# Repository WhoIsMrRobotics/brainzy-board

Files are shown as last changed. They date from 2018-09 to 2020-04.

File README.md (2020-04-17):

# Brainzy Board

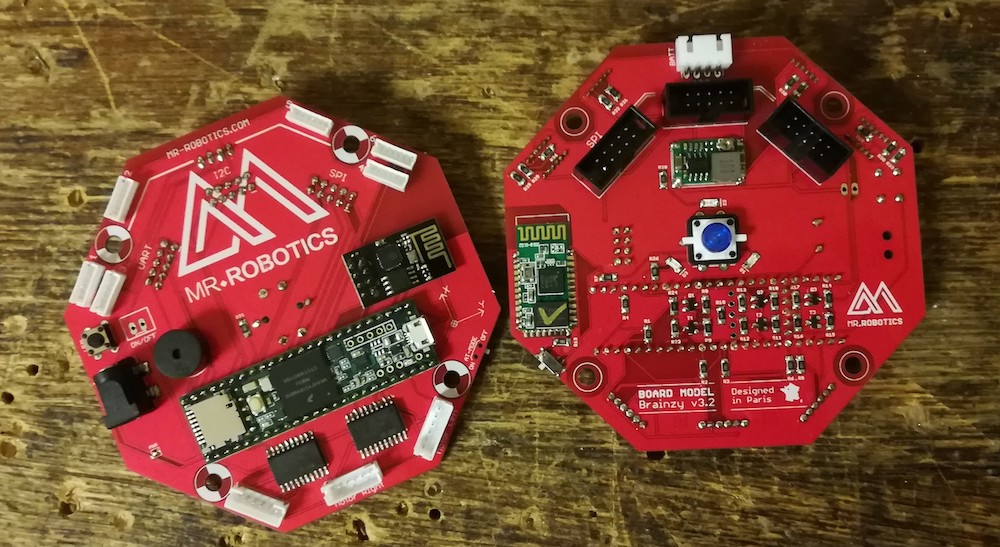
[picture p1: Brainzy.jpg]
Brainzy Board


Il s'agit d'une alternative aux cartes Arduino pour facilement construire son propre robot différentiel ou omnidirectionel. Basé sur une [Teensy 3.5](https://www.pjrc.com/store/teensy35.html), la Brainzy board se programme en C++ à travers l'[IDE Arduino](https://www.arduino.cc/en/Main/Software) à l'aide de la [bibliothèque Brainzy](https://github.com/WhoIsMrRobotics/brainzy-library). De nombreux modules peuvent être ajoutés à la carte pour étendre la complexité de vos créations.

Il existe deux types de modules :
* Les *Widgets*, dont la connection se fait par des connecteurs magnétiques et la communication via un bus I2C ;
* Les *extensions*, dont la connection se fait par des connecteurs standards et la communication via des bus SPI, UART, et/ou I2C.

Pour plus d'information, consultez notre site [www.mr-robotics.com](https://www.mr-robotics.com/).

**Caractéristiques de la Brainzy Board**

* *Mode d'utilisation :* 2 choix possibles pour le déplacement du robot : entrainement différenciel (2 roues) ou entrainement omnidirectionel (3 roues)
* *Dimensions de la carte :* 100mm x 100mm (forme hexagonale)
* *Moyens de communication :* USB, Bluetooth et Wifi

**Ports Entrées/Sorties**

* 1 port micro-USB
* 8 ports I2C, 3 ports SPI, 2 ports UART
* 3 ports pour des moteurs DC dotés de codeurs incrémentaux (deux channels)
* 1 lecteur de carte nano-SD
* 1 port pour vérifier l'état de charge de la batterie (jusqu'à 3 cellules)
* 1 Buzzer
* 1 interrupteur programmable
* 2 LEDs programmables

**Modules intégrés**

* 1 Module bluetooth (HC-05)
* 1 Module Wifi (ESP8266-01)

**Exemples de Widgets associés**

* IMU : accéléromètre 3 axes + gyroscope 3 axes (MPU-6050)
* Système d'éclairage : NeoPixels (WS2812B)
* Télémètre à ultrasons : Sonar (HC-SR04)
* Télémètre infrarouge : Sharp (GP2Y0A41SK0F)
* ...

**Exemples d'extensions associées**

* Bras poly-articulé
* Système de webcam pilotée
* Télécomande bluetooth
* Écran tactile
* ...

## Comment l'obtenir ?

Vous pouvez la commander en [nous contactant](mailto:bonjour@mr-robotics.com) ou suivre les étapes suivantes :
1. Réalisez le PCB à l'aide des fichiers GERBER.
2. Commandez les composants répertoriés dans le fichier BOM, puis soudez les.
3. Soudez une Teensy 3.5 en faisant attention aux indications suivantes.
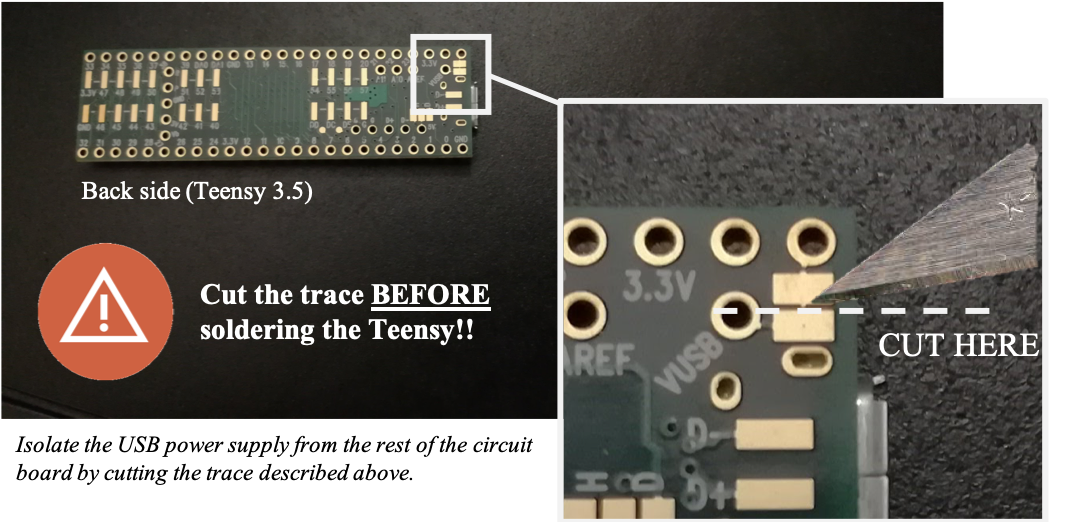
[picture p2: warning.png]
Warning cut VUSB trace


## Quelques tutoriels

* Pour obtenir un modèle CAO de la carte, consultez [ce lien](https://www.youtube.com/watch?v=ekHAkWB-WTM).
* Pour générer les fichiers Gerber nécessaire à la production du PCB, consultez [ce lien](https://learn.sparkfun.com/tutorials/designing-pcbs-advanced-smd/gerber-generation).

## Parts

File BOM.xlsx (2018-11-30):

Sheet: PCB - Brainzy 3.2.1
PCB
Size | 10cm x 10cm
Soldermask Color | Red
Silkscreen Legend Color | White
Thickness | 1.6mm
Penalization | Single board, no penalization
Layer | 2
Quantity | 100
Outer Copper Thickness | 1oz, 35um
Surface Finish | HASL
Material | FR4
Smallest Hole | 0.25mm
Min. Tracing/Spacing | 0.15mm
PCBA
Number of SMD items | 62
Number of TH items | 18
Number of BGA / QFN / Leadless items | 0
Quantity | 100

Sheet: BOM - Brainzy 3.2.1
Manufacturer | Manufacturer Part Number | Designator | Qty | Description | Case | SMD, BGA, LCC, or TH | Top/Bottom | Points | Total points | Comment
Yageo | RC1206FR-071KL | R1; R2; R3; R4; R5; R6; R20 | 7 | Résistance 1k (tolérence 1%) | 1206 | SMD | Bottom | 2 | 14
Yageo | RC1206FR-0710KL | R22 | 1 | Résistance 10k (tolérence 1%) | 1206 | SMD | Bottom | 2 | 2
Yageo | RC1206FR-0710KL | R19 | 1 | Résistance 10k (tolérence 1%) | 1206 | SMD | Top | 2 | 2
Yageo | RC1206FR-07470KL | R8; R9; R10; R11; R12; R14; R15; R16; R18; R24; R25; R30; R31; R34; R35 | 15 | Résistance 470k (tolérence 1%) | 1206 | SMD | Bottom | 2 | 30
Yageo | RC1206FR-07150KL | R13; R17; R23; R28; R29; R32; R33; R36 | 8 | Résistance 150k (tolérence 1%) | 1206 | SMD | Bottom | 2 | 16
Yageo | RC1206FR-07470RL | R7; R26 | 2 | Résistance 470 (tolérence 1%) | 1206 | SMD | Bottom | 2 | 4
Yageo | RC1206FR-07470RL | R21 | 1 | Résistance 470 (tolérence 1%) | 1206 | SMD | Top | 2 | 2
ON Semiconductor | BSS84LT1G | T1; T2; T3 | 3 | Mosfet canal P | SOT23 | SMD | Bottom | 3 | 9
ON Semiconductor | BSS138LT1G | Q1; Q2; Q3 | 3 | Mosfet canal N | SOT23 | SMD | Bottom | 3 | 9
TE Connectivity | MLL1200S | S1 | 1 | Commutateur à glissière |  | SMD | Bottom | 7 | 7
DIALIGHT | 598-8210-107F | D2 | 1 | Led rouge | 1206 | SMD | Bottom | 2 | 2
DIALIGHT | 598-8291-107F | D3 | 1 | Led bleu | 1206 | SMD | Bottom | 2 | 2
DIALIGHT | 598-8270-107F | D1 | 1 | Led verte | 1206 | SMD | Bottom | 2 | 2
STMicroelectronics | L293DD | U1; U2 | 2 | Pont en H | SOIC-20 | SMD | Top | 20 | 40
JST | B6B-ZR(LF)(SN) | SENSOR1; SENSOR2; SENSOR3; SENSOR4; SENSOR5; SENSOR6 | 6 | Connecteur ZH 6 pins | - | TH | Top | 6 | 36
JST | B6B-PH-K-S(LF)(SN) | MOT_LEFT; MOT_RIGHT; MOT_FRONT | 3 | Connecteur PH 6 pins | - | TH | Top | 6 | 18
JST | S4B-XH-A(LF)(SN) | BATT | 1 | Connecteur XH 4 pins coudé | - | TH | Bottom | 4 | 4
JST | B2B-XH-A(LF)(SN) | ON/OFF | 0 | Connecteur XH 2 pins | - | TH | Top | 2 | 0
Würth Elektronik | 694108106102 | J7 | 1 | Connecteur jack alimentation | - | SMD | Top | 4 | 4
C&K Components | PTS645SL43-2-LFS | RST | 1 | Intérupteur | - | TH | Top | 4 | 4
Amphenol | T821110A1S100CEU | EXT1; EXT2; EXT3 | 3 | Connecteur 5x2 pins | - | TH | Bottom | 10 | 30
IMO PRECISION CONTROLS | 41.T70P015H-LF | LS1 | 1 | Transducteur passif | - | TH | Top | 2 | 2
HC | HC-05 | U3 | 1 | Module bluetooth | - | SMD | Bottom | 34 | 34 | Must be a HC-05 (not a HC-06)
Espressif Systems | ESP8266 (ESP-01) | U$6 | 1 | Module Wifi | - | TH | Top | 8 | 8
PJRC | Teensy 3.5 | U$1 | 1 | Microcontrôleur | - | TH | Top | 53 | 53 | https://www.pjrc.com/store/teensy35.html (Cut the VUSB trace before soldering the Teensy)
? | TSD1265 | S2 | 1 | Bouton LED bleu | - | TH | Bottom | 6 | 6 | https://www.sparkfun.com/products/10443
Monolithic Power Systems | MP2307DN-LF | BK | 1 | - | SOIC8N | SMD | Bottom | 8 | 8
Kemet | C1210C106M4PACTU | C4; C5 | 2 | Condensateur 10uF en céramique | 1210 | SMD | Bottom | 2 | 4
AVX | 06031C103K4Z2A | C6 | 1 | Condensateur 10nF | 0603 | SMD | Bottom | 2 | 2
AVX | 0603YC104K4T4A | C3 | 1 | Condensateur 0.1uF | 0603 | SMD | Bottom | 2 | 2
AVX | 06035C332KAT2A | C7 | 1 | Condensateur 3.3nF | 0603 | SMD | Bottom | 2 | 2
Yageo | CC0805MKX5R5BB226 | C1; C2 | 2 | Condensateur 22uF en céramique | 0805 | SMD | Bottom | 2 | 4
Abracon | ASPI-0630LR-100M-T15 | L1 | 1 | Inductance 10uH | 0630 | SMD | Bottom | 2 | 2
Vishay | CRCW0603100KFKEA | R39 | 1 | Résistance 100k (tolérence 1%) | 0603 | SMD | Bottom | 2 | 2
Vishay | CRCW060344K2FKEA | R38 | 1 | Résistance 44,2k (tolérence 1%) | 0603 | SMD | Bottom | 2 | 2
Vishay | CRCW060310K0FKEA | R37 | 1 | Résistance 10k (tolérence 1%) | 0603 | SMD | Bottom | 2 | 2
Vishay | CRCW06036K80FKEA | R27 | 1 | Résistance 6.8k (tolérence 1%) | 0603 | SMD | Bottom | 2 | 2

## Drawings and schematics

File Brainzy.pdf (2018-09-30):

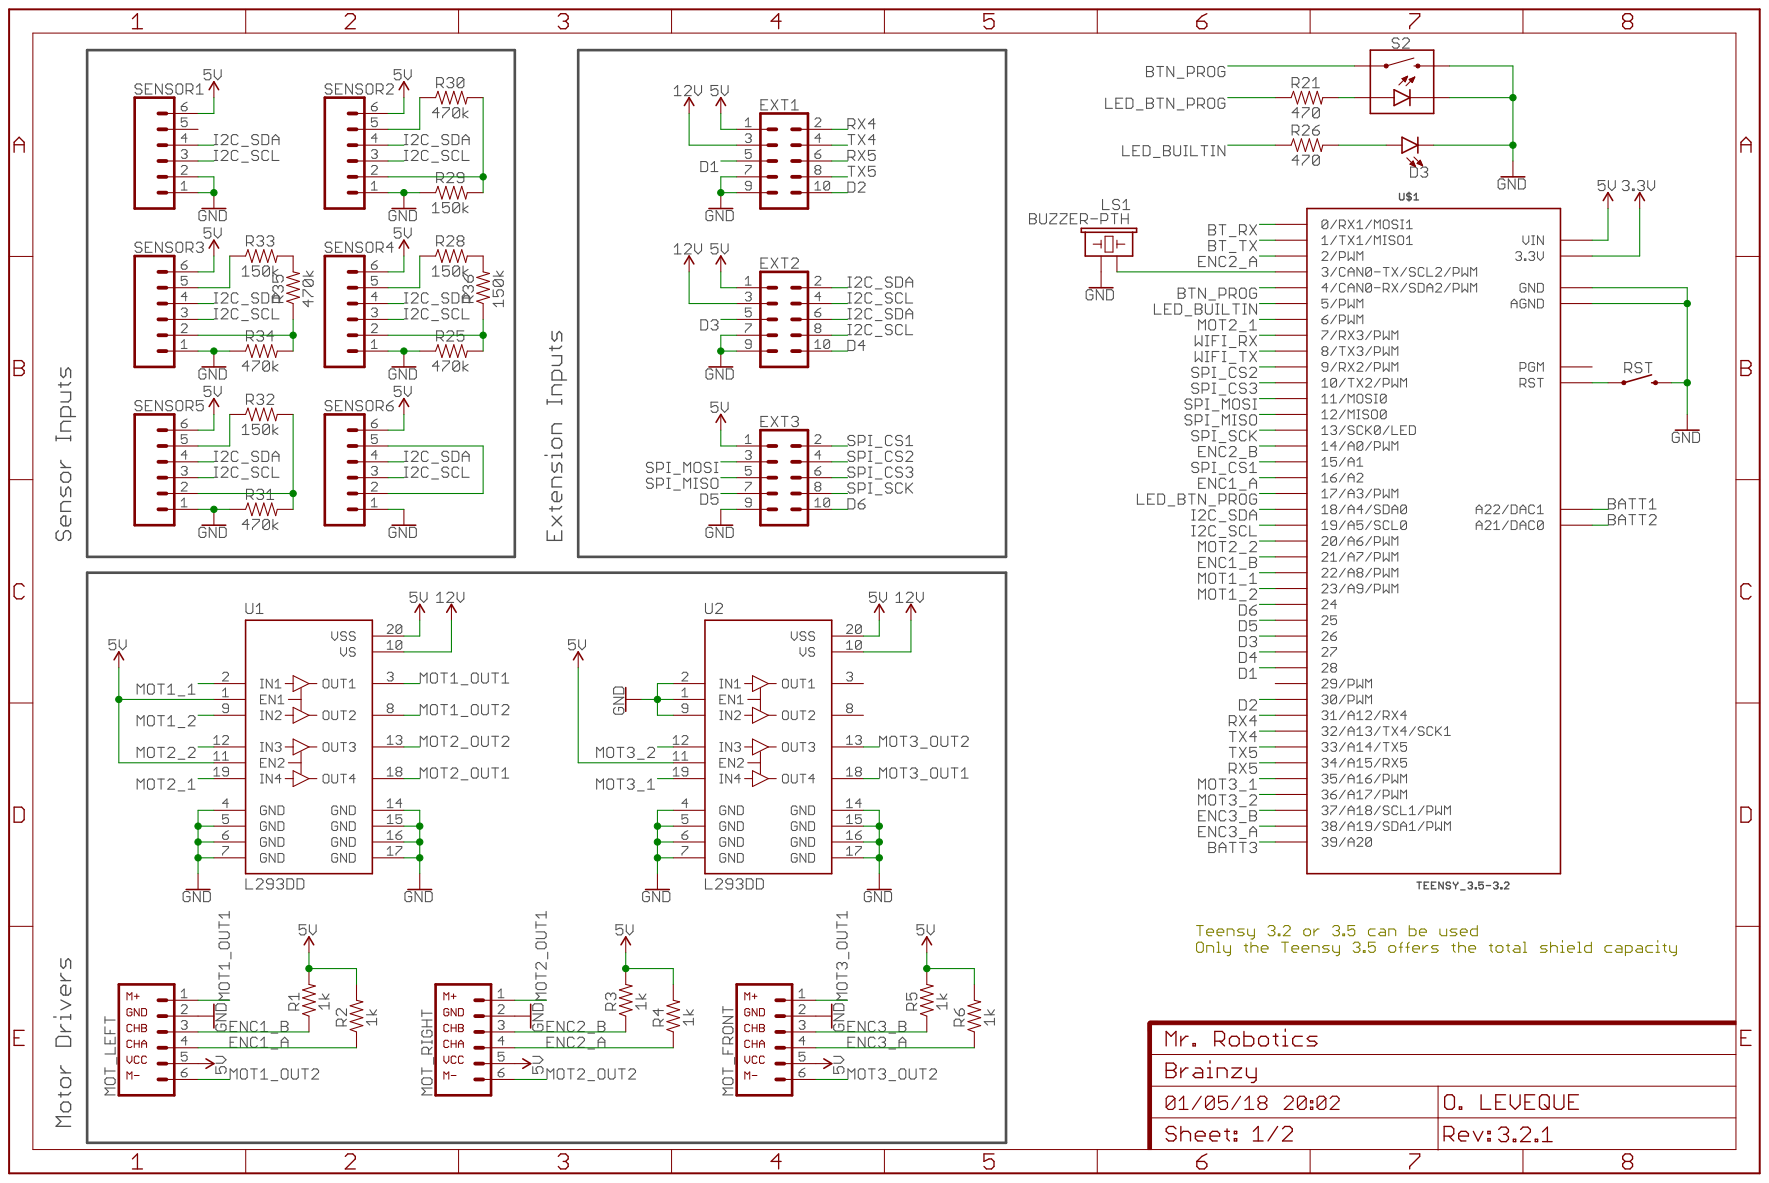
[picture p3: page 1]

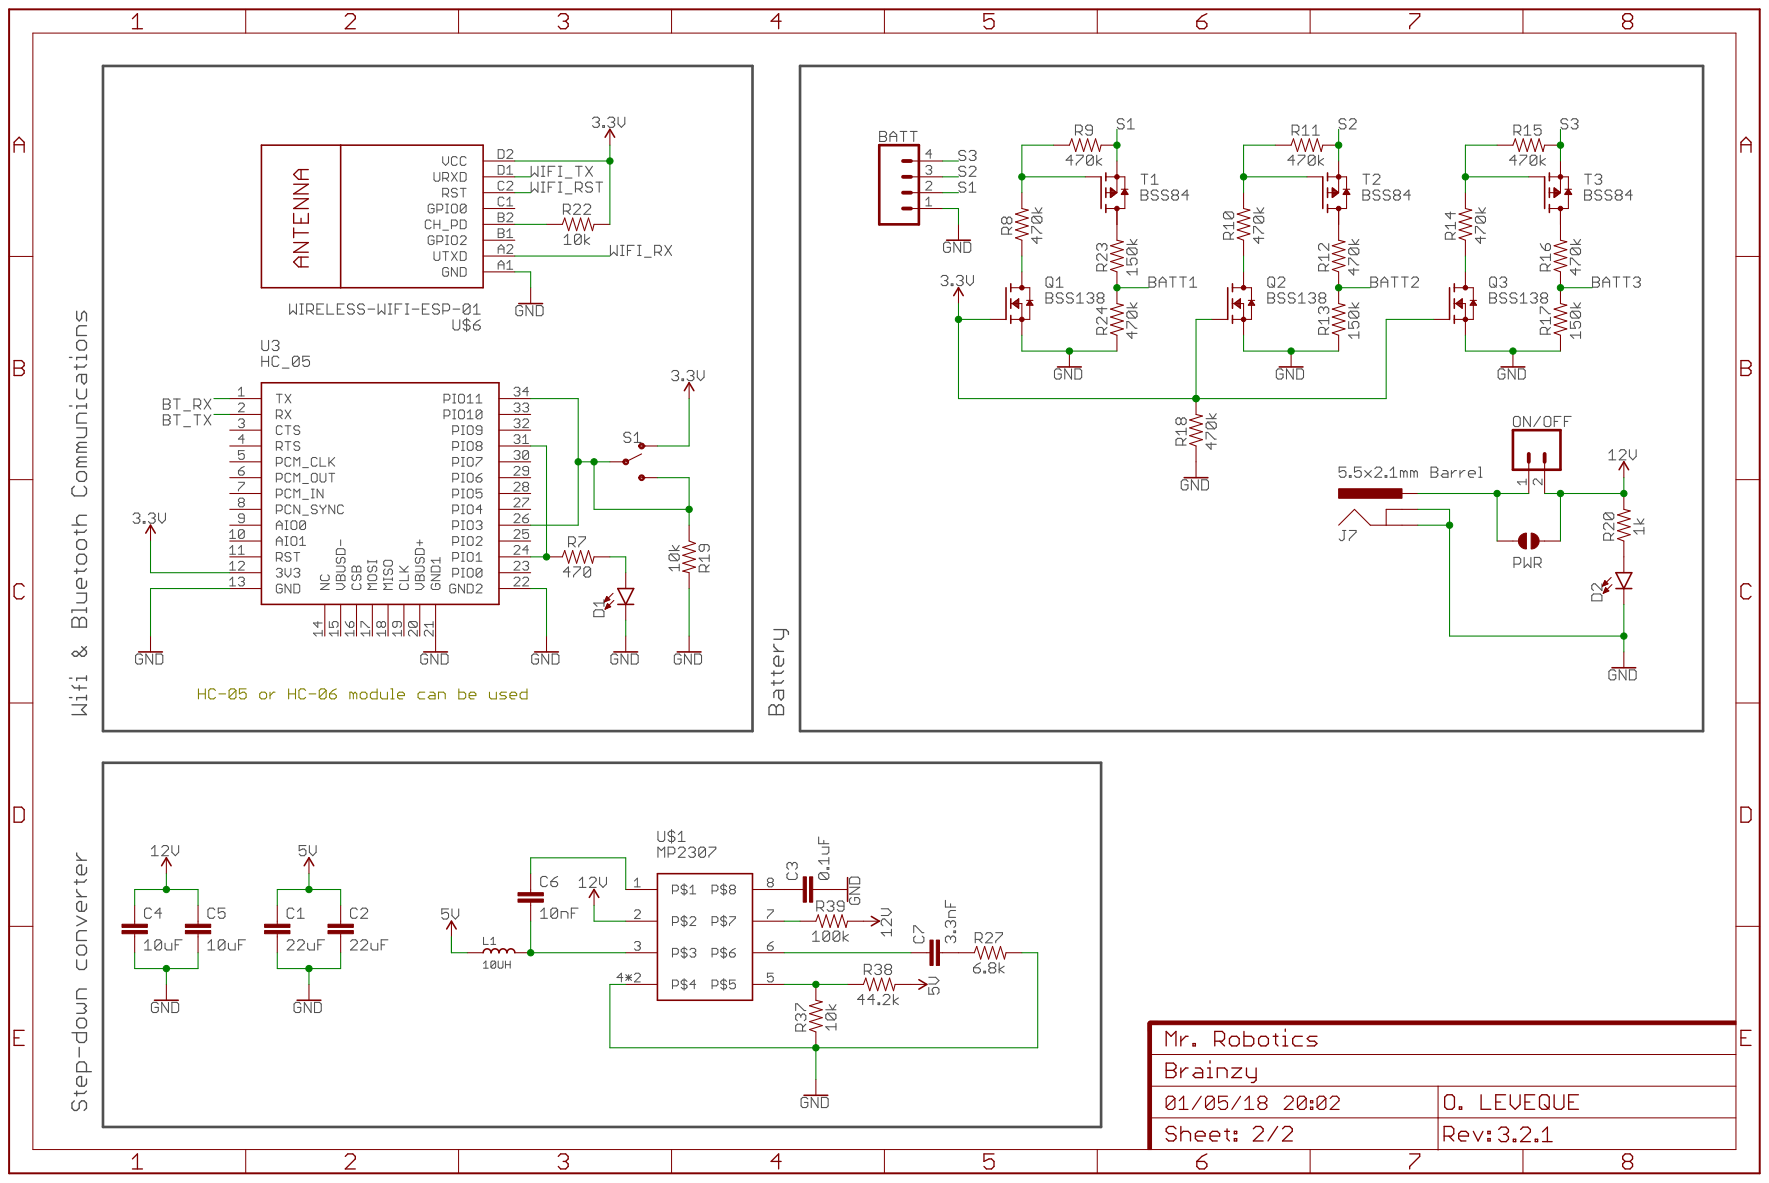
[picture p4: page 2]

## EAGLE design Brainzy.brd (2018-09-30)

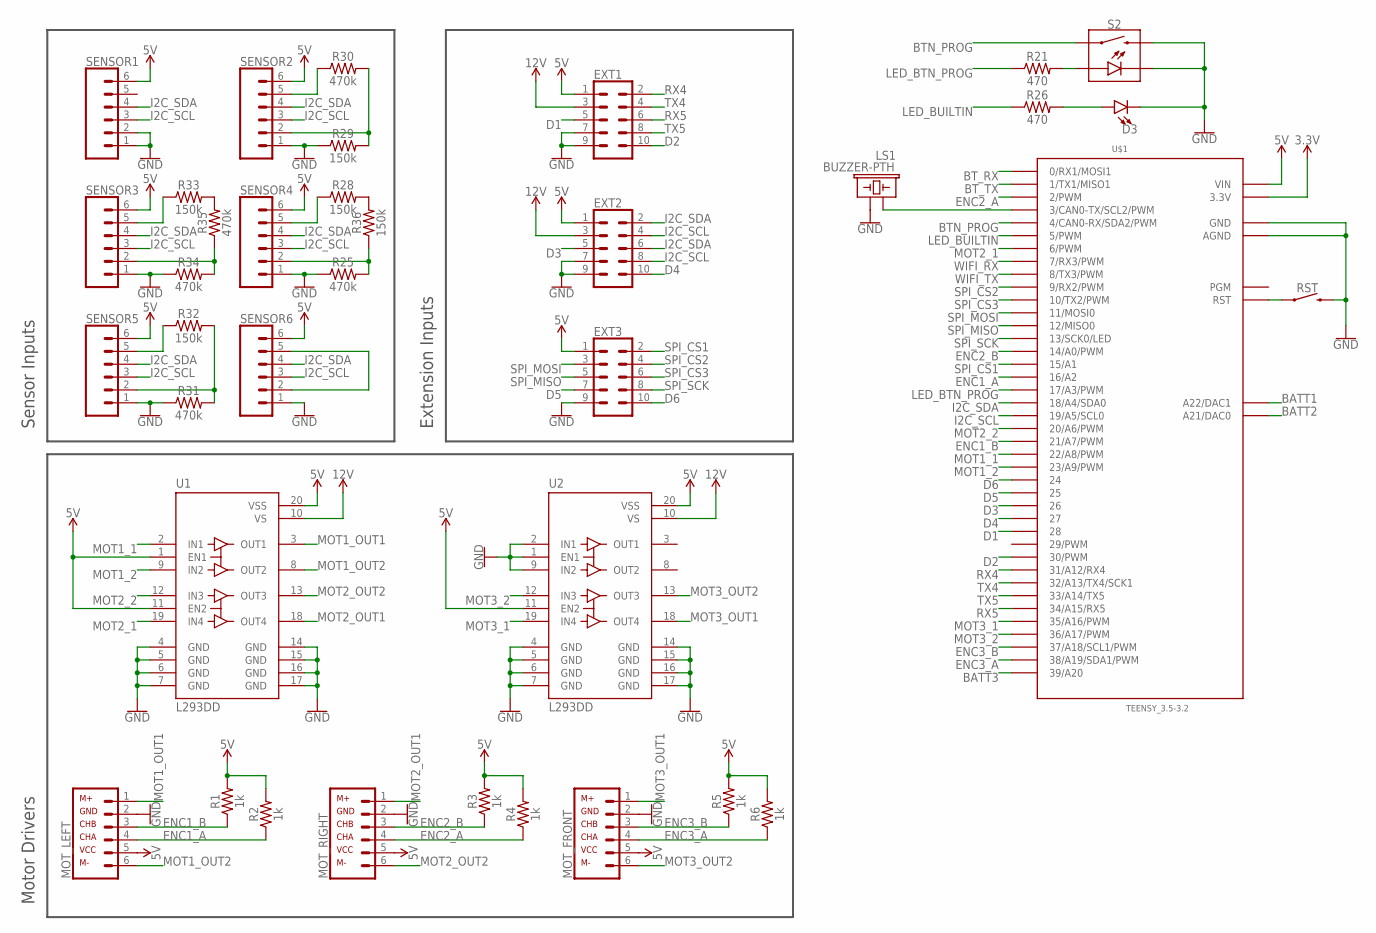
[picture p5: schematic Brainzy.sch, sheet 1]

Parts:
D3: LED-FKIT-1206; FKIT-LED-1206
EXT1, EXT2, EXT3: CONN_05X2SHD_LOCK; 2X5-SHROUDED_LOCK
LS1: BUZZER-PTH; BUZZER-12MM
MOT_FRONT: DC-MOTOR-CONNECTOR; JST-PH6
MOT_LEFT: DC-MOTOR-CONNECTOR; JST-PH6
MOT_RIGHT: DC-MOTOR-CONNECTOR; JST-PH6
R1, R2, R3, R4, R5, R6: 1k; 1206
R21, R26: 470; 1206
R25, R30, R31, R34, R35: 470k; 1206
R28, R29, R32, R33, R36: 150k; 1206
RST: MOMENTARY-SWITCH-SPST-PTH-6.0MM; TACTILE_SWITCH_PTH_6.0MM
S2: MOMENTARY-SWITCH-SPST-LED-PTH-12MM; TACTILE_SWITCH_LED_PTH_12MM
SENSOR1, SENSOR2, SENSOR3, SENSOR4, SENSOR5, SENSOR6: JST-ZH6
U1, U2: L293DD; SOIC127P1033X265-20N
U$1: TEENSY_3.5-3.2

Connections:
3.3V: U$1.3.3V, U$1.3.3V1 (3.3V), U$1.3.3V2 (3.3V), U$1.3.3V3 (3.3V); also elsewhere on the board
5V: EXT1.1, EXT2.1, EXT3.1, MOT_FRONT.5 (5-CHA), MOT_LEFT.5 (5-CHA), MOT_RIGHT.5 (5-CHA), R1.2, R2.2, R3.2, R4.2, R5.2, R6.2, SENSOR1.6, SENSOR2.6, SENSOR3.6, SENSOR4.6, SENSOR5.6, SENSOR6.6, U1.1 (EN1), U1.11 (EN2), U1.20 (VSS), U2.11 (EN2), U2.20 (VSS), U$1.VIN; also elsewhere on the board
12V: EXT1.3, EXT2.3, U1.10 (VS), U2.10 (VS); also elsewhere on the board
BATT1: U$1.A22 (A22/DAC1); also elsewhere on the board
BATT2: U$1.A21 (A21/DAC0); also elsewhere on the board
BATT3: U$1.39/A20; also elsewhere on the board
BTN_PROG: S2.4 (1), U$1.4 (4/CAN0-RX/SDA2/PWM)
BT_RX: U$1.0 (0/RX1/MOSI1); also elsewhere on the board
BT_TX: U$1.1 (1/TX1/MISO1); also elsewhere on the board
BUZZER: LS1.+ (1), U$1.3 (3/CAN0-TX/SCL2/PWM)
D1: EXT1.5, U$1.28
D2: EXT1.10, U$1.30 (30/PWM)
D3: EXT2.5, U$1.26
D4: EXT2.10, U$1.27
D5: EXT3.7, U$1.25
D6: EXT3.10, U$1.24
ENC1_A: MOT_LEFT.4 (4-GND), R2.1, U$1.16/A2
ENC1_B: MOT_LEFT.3 (3-VCC), R1.1, U$1.21/A7 (21/A7/PWM)
ENC2_A: MOT_RIGHT.4 (4-GND), R4.1, U$1.2 (2/PWM)
ENC2_B: MOT_RIGHT.3 (3-VCC), R3.1, U$1.14/A0 (14/A0/PWM)
ENC3_A: MOT_FRONT.4 (4-GND), R6.1, U$1.38/A19 (38/A19/SDA1/PWM)
ENC3_B: MOT_FRONT.3 (3-VCC), R5.1, U$1.37/A18 (37/A18/SCL1/PWM)
GND: D3.C, EXT1.7, EXT1.9, EXT2.7, EXT2.9, EXT3.9, LS1.- (2), MOT_FRONT.2 (2-M+), MOT_LEFT.2 (2-M+), MOT_RIGHT.2 (2-M+), R25.1, R29.1, R31.1, R34.1, RST.3 (2), S2.2, S2.C, SENSOR1.1, SENSOR1.2, SENSOR2.1, SENSOR3.1, SENSOR4.1, SENSOR5.1, SENSOR6.1, U1.4 (GND), U1.5 (GND), U1.6 (GND), U1.7 (GND), U1.14 (GND), U1.15 (GND), U1.16 (GND), U1.17 (GND), U2.1 (EN1), U2.2 (IN1), U2.4 (GND), U2.5 (GND), U2.6 (GND), U2.7 (GND), U2.9 (IN2), U2.14 (GND), U2.15 (GND), U2.16 (GND), U2.17 (GND), U$1.AGND, U$1.GND, U$1.GND1 (GND), U$1.GND2 (GND), U$1.GND3 (GND); also elsewhere on the board
I2C_SCL: EXT2.4, EXT2.8, SENSOR1.3, SENSOR2.3, SENSOR3.3, SENSOR4.3, SENSOR5.3, SENSOR6.3, U$1.19/A5 (19/A5/SCL0)
I2C_SDA: EXT2.2, EXT2.6, SENSOR1.4, SENSOR2.4, SENSOR3.4, SENSOR4.4, SENSOR5.4, SENSOR6.4, U$1.18/A4 (18/A4/SDA0)
LED_BTN_PROG: R21.1, U$1.17/A3 (17/A3/PWM)
LED_BUILTIN: R26.1, U$1.5 (5/PWM)
MOT1_1: U1.2 (IN1), U$1.22/A8 (22/A8/PWM)
MOT1_2: U1.9 (IN2), U$1.23/A9 (23/A9/PWM)
MOT1_OUT1: MOT_LEFT.1 (1-M-), U1.3 (OUT1)
MOT1_OUT2: MOT_LEFT.6 (6-CHB), U1.8 (OUT2)
MOT2_1: U1.19 (IN4), U$1.6 (6/PWM)
MOT2_2: U1.12 (IN3), U$1.20/A6 (20/A6/PWM)
MOT2_OUT1: MOT_RIGHT.1 (1-M-), U1.18 (OUT4)
MOT2_OUT2: MOT_RIGHT.6 (6-CHB), U1.13 (OUT3)
MOT3_1: U2.19 (IN4), U$1.35/A16 (35/A16/PWM)
MOT3_2: U2.12 (IN3), U$1.36/A17 (36/A17/PWM)
MOT3_OUT1: MOT_FRONT.1 (1-M-), U2.18 (OUT4)
MOT3_OUT2: MOT_FRONT.6 (6-CHB), U2.13 (OUT3)
unnamed: D3.A, R26.2
unnamed: R21.2, S2.A
unnamed: SENSOR6.2, SENSOR6.5
unnamed: R25.2, R36.1, SENSOR4.2
unnamed: R28.1, SENSOR4.5
unnamed: R31.2, R32.2, SENSOR5.2
unnamed: R32.1, SENSOR5.5
unnamed: R29.2, R30.2, SENSOR2.2
unnamed: R30.1, SENSOR2.5
unnamed: R33.2, R35.2
unnamed: R34.2, R35.1, SENSOR3.2
unnamed: R33.1, SENSOR3.5
unnamed: R28.2, R36.2
RST: RST.1, U$1.RST_3.5 (RST)
RX4: EXT1.2, U$1.31/A12 (31/A12/RX4)
RX5: EXT1.6, U$1.34/A15 (34/A15/RX5)
SPI_CS1: EXT3.2, U$1.15/A1
SPI_CS2: EXT3.4, U$1.9 (9/RX2/PWM)
SPI_CS3: EXT3.6, U$1.10 (10/TX2/PWM)
SPI_MISO: EXT3.5, U$1.12 (12/MISO0)
SPI_MOSI: EXT3.3, U$1.11 (11/MOSI0)
SPI_SCK: EXT3.8, U$1.13 (13/SCK0/LED)
TX4: EXT1.4, U$1.32/A13 (32/A13/TX4/SCK1)
TX5: EXT1.8, U$1.33/A14 (33/A14/TX5)
WIFI_RX: U$1.7 (7/RX3/PWM); also elsewhere on the board
WIFI_TX: U$1.8 (8/TX3/PWM); also elsewhere on the board

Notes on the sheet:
Motor Drivers
Sensor Inputs
Extension Inputs

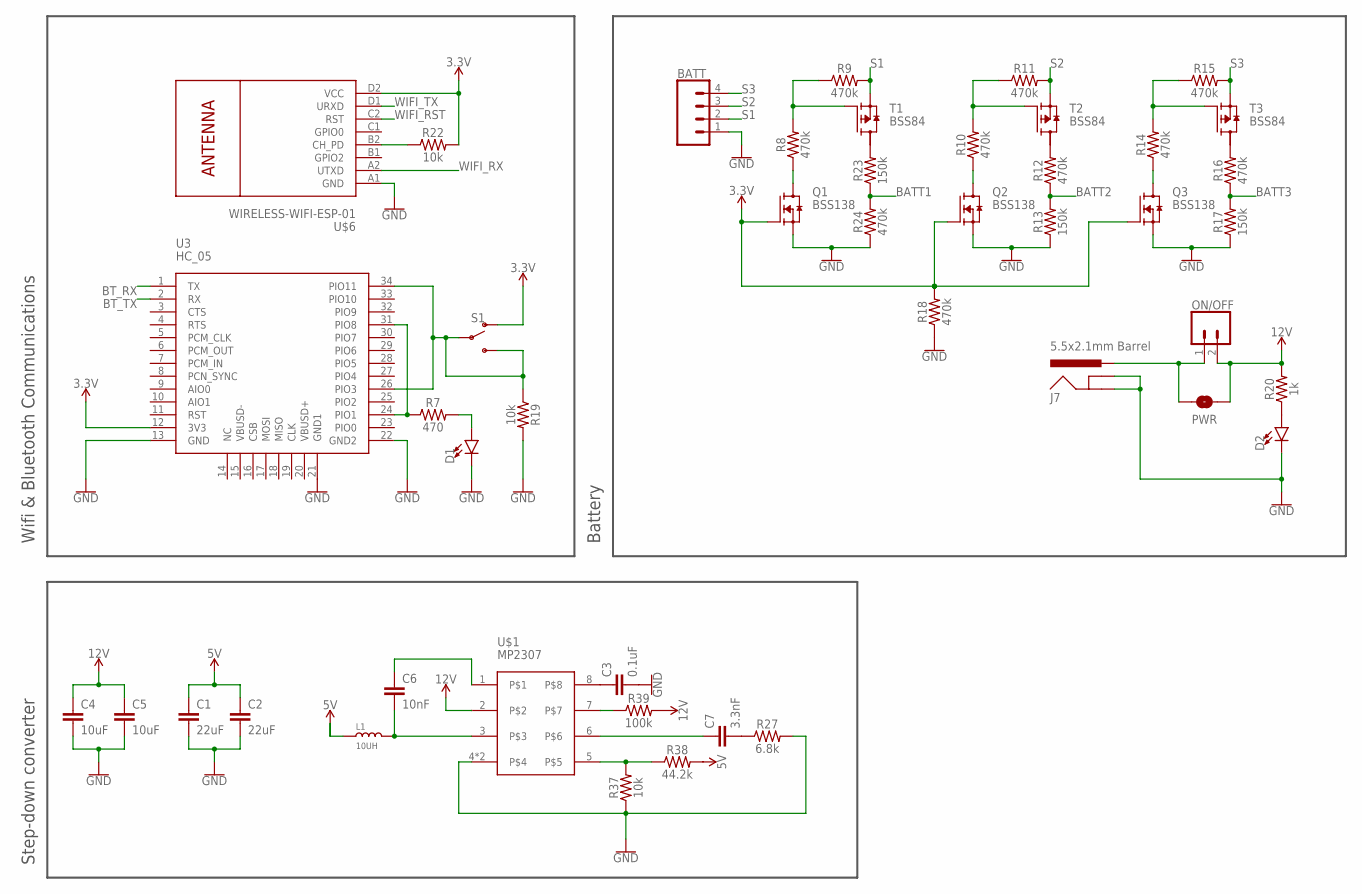
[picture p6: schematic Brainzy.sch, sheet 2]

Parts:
BATT: CONN_04LOCK_LONGPADS; 1X04_LOCK_LONGPADS
BK: MP2307; SOIC127P600X170-9N
C1, C2: 22uF; 0805
C3: 0.1uF; 0603
C4, C5: 10uF; 1210
C6: 10nF; 0603
C7: 3.3nF; 0603
D1, D2: LED-FKIT-1206; FKIT-LED-1206
J7: 5.5x2.1mm Barrel; POWER_JACK_SMD
L1: 10UH; SMD-2P-L6.0XW6.0XH3.0MM
ON/OFF: JST-XH-02-PIN-LONG-PAD; JST-XH-02-PACKAGE-LONG-PAD
PWR: JUMPER-SMT_2_NO_SILK; SMT-JUMPER_2_NO_SILK
Q1, Q2, Q3: BSS138; SOT23
R7: 470; 1206
R8, R9, R10, R11, R12, R14, R15, R16, R18, R24: 470k; 1206
R13, R17, R23: 150k; 1206
R19, R22: 10k; 1206
R20: 1k; 1206
R27: 6.8k; 0603
R37: 10k; 0603
R38: 44.2k; 0603
R39: 100k; 0603
S1: SWITCH-SPDT-SMD-RIGHT-ANGLE; SWITCH_SPST_SMD_A
T1, T2, T3: BSS84; SOT23
U3: HC_05; BLUETOOTH_SMD
U$6: WIRELESS-WIFI-ESP-01

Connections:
3.3V: Q1.1 (G), Q2.1 (G), Q3.1 (G), R18.2, R22.2, S1.1 (O), U3.12 (3V3), U$6.D2 (VCC); also elsewhere on the board
5V: C1.1, C2.1, L1.1, R38.2; also elsewhere on the board
12V: BK.2, C4.1, C5.1, ON/OFF.2, PWR.2, R20.2, R39.2; also elsewhere on the board
BATT1: R23.1, R24.2; also elsewhere on the board
BATT2: R12.1, R13.2; also elsewhere on the board
BATT3: R16.1, R17.2; also elsewhere on the board
BT_RX: U3.1 (TX); also elsewhere on the board
BT_TX: U3.2 (RX); also elsewhere on the board
GND: BATT.1, BK.4, BK.9, C1.2, C2.2, C3.2, C4.2, C5.2, D1.C, D2.C, J7.GND (GNDBREAK), J7.P$4 (GND), Q1.2 (S), Q2.2 (S), Q3.2 (S), R13.1, R17.1, R18.1, R19.2, R24.1, R27.2, R37.1, U3.13 (GND), U3.21 (GND1), U3.22 (GND2), U$6.A1 (GND); also elsewhere on the board
unnamed: R12.2, T2.3 (D)
unnamed: D2.A, R20.1
unnamed: R22.1, U$6.B2 (CH_PD)
unnamed: R8.2, R9.1, T1.1 (G)
unnamed: Q1.3 (D), R8.1
unnamed: R16.2, T3.3 (D)
unnamed: R10.2, R11.1, T2.1 (G)
unnamed: BK.7, R39.1
unnamed: R7.1, U3.24 (PIO1), U3.31 (PIO8)
unnamed: D1.A, R7.2
unnamed: Q2.3 (D), R10.1
unnamed: R14.2, R15.1, T3.1 (G)
unnamed: Q3.3 (D), R14.1
unnamed: J7.VIN0 (PWR), ON/OFF.1, PWR.1
unnamed: R19.1, S1.2, S1.3 (S), U3.26 (PIO3), U3.34 (PIO11)
unnamed: R23.2, T1.3 (D)
unnamed: BK.5, R37.2, R38.1
unnamed: BK.8, C3.1
unnamed: BK.6, C7.1
unnamed: BK.3, C6.2, L1.2
unnamed: C7.2, R27.1
unnamed: BK.1, C6.1
S1: BATT.2, R9.2, T1.2 (S)
S2: BATT.3, R11.2, T2.2 (S)
S3: BATT.4, R15.2, T3.2 (S)
WIFI_RST: U$6.C2 (RST)
WIFI_RX: U$6.A2 (UTXD); also elsewhere on the board
WIFI_TX: U$6.D1 (URXD); also elsewhere on the board

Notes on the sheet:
Wifi & Bluetooth Communications
Battery
Step-down converter

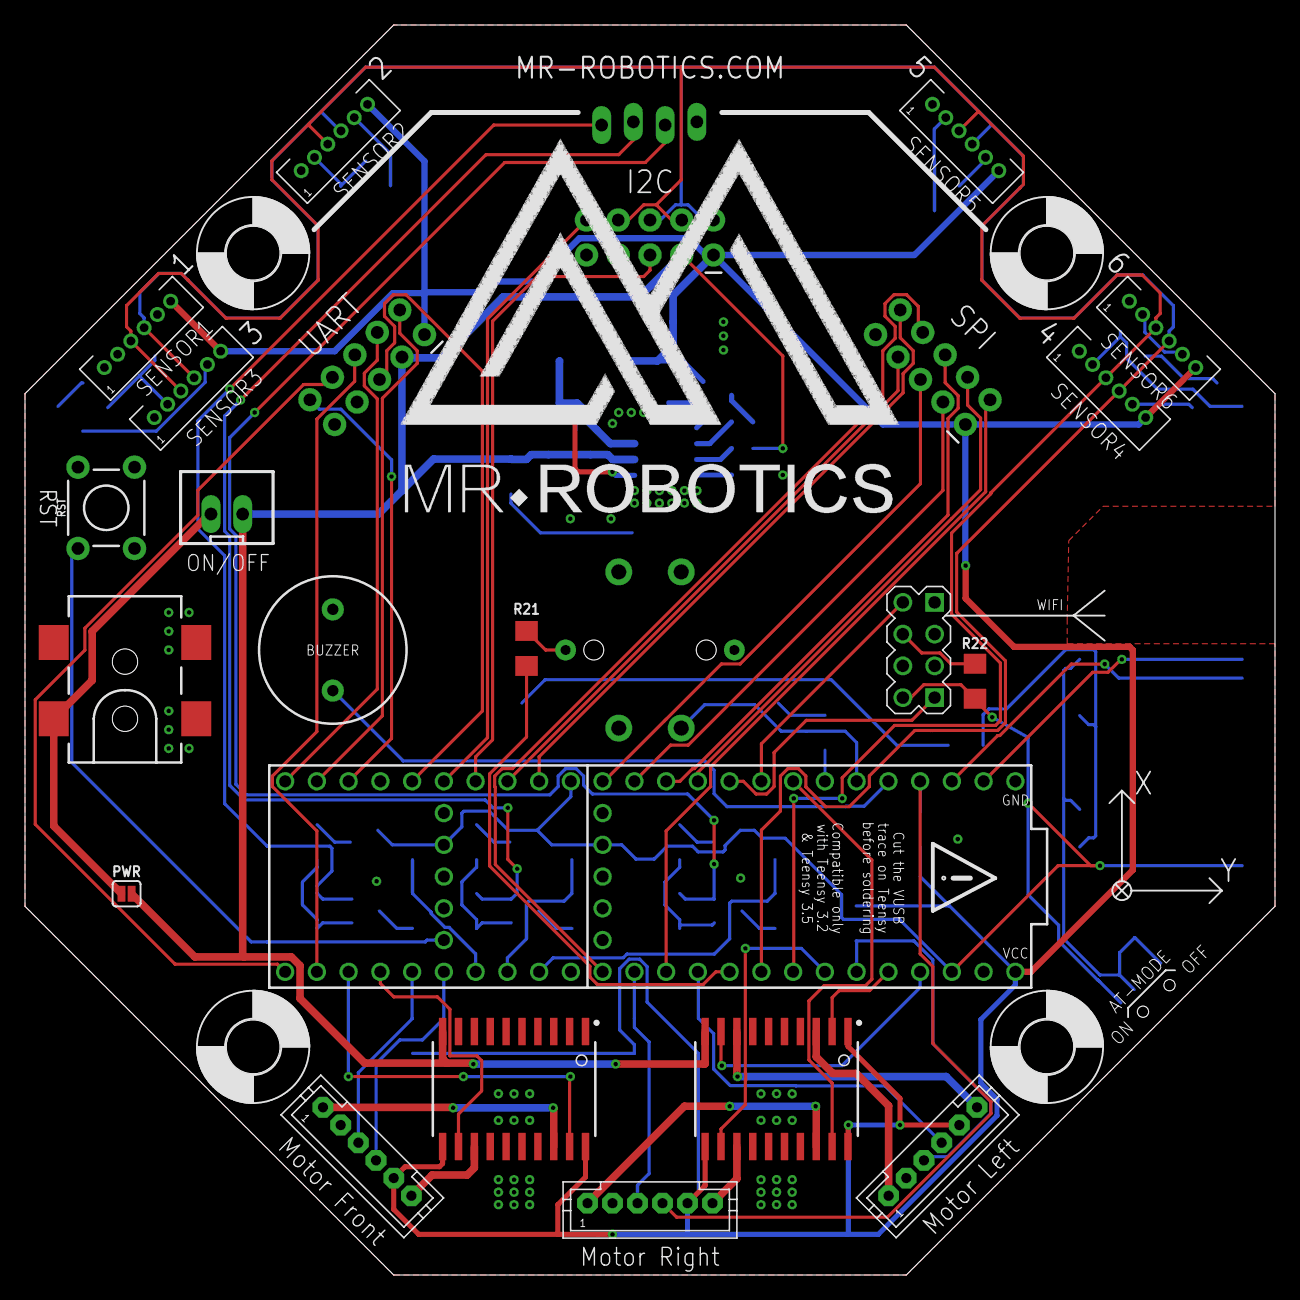
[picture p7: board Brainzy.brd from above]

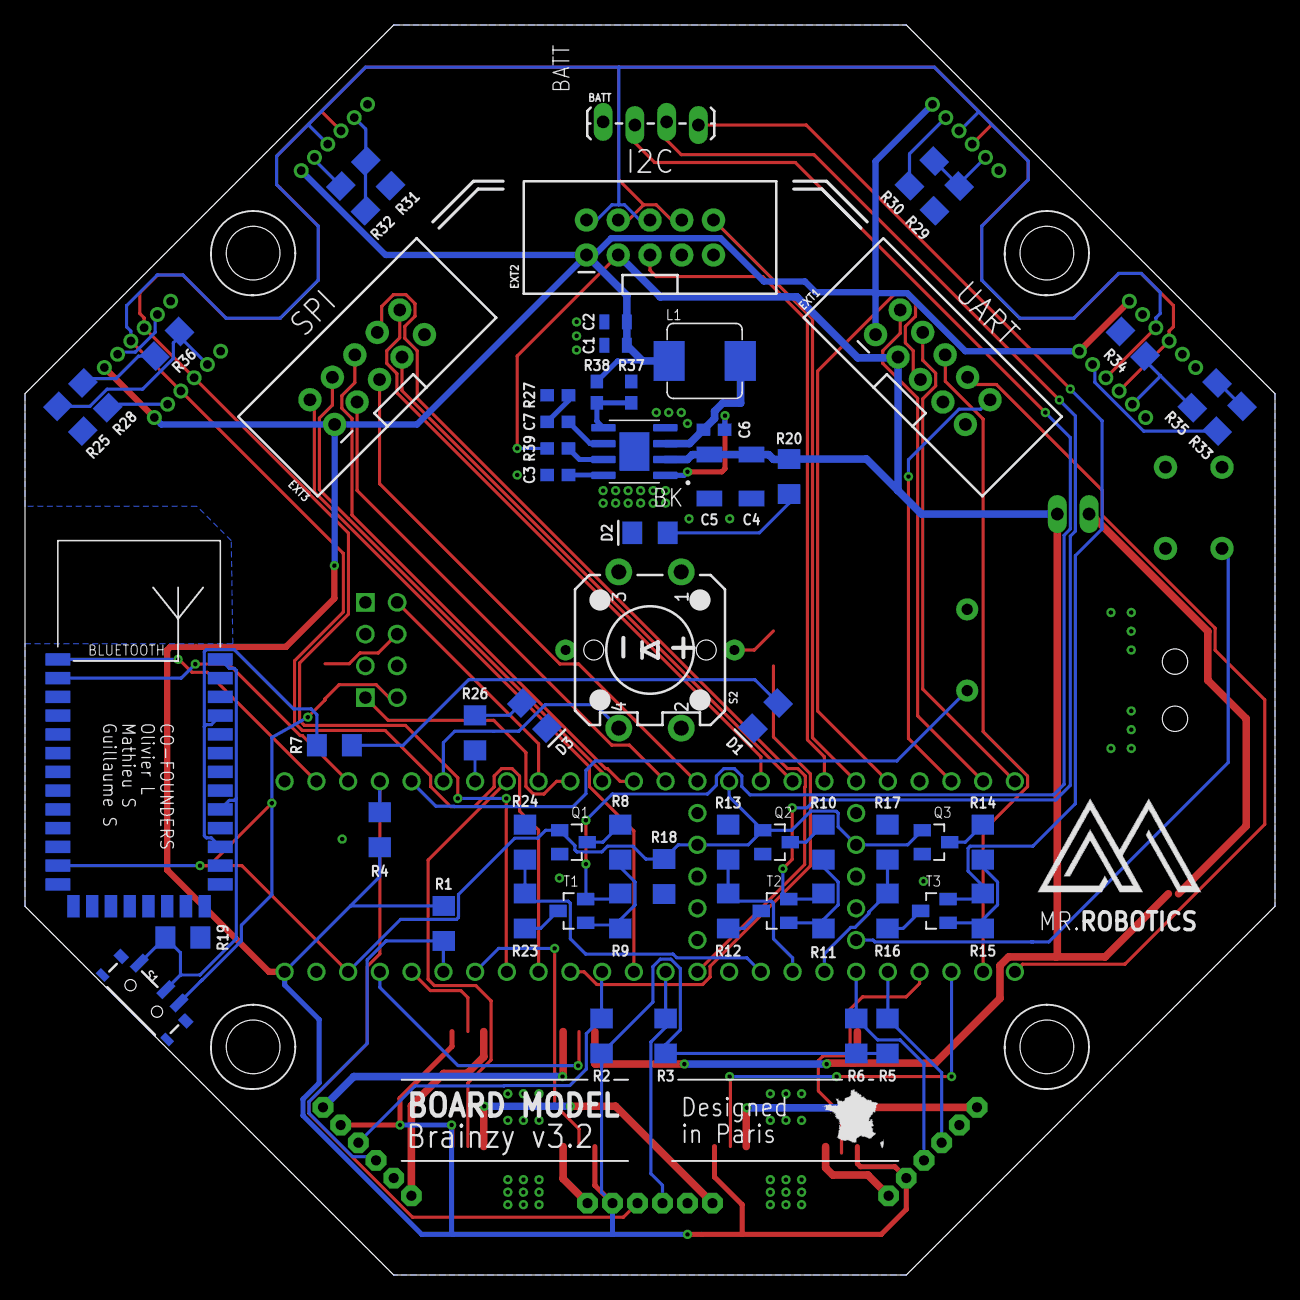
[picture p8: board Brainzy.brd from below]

Board: 2 copper layers, 100.0 x 100.0 mm, 90 parts (64 on the bottom side), 90 nets.

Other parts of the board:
U$3: LOGO_FR
U$4: M_40MM
U$8, U$9, U$10, U$11: 4,3
U$12: LOGO_M
U$13: NAME_40MM

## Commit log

2018-09-30 Upload Brainzy v1.0
    [Brainzy.brd, Brainzy.sch]
2018-09-30 Upload Brainzy v1.1
    [Brainzy.brd, Brainzy.sch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]
2018-09-30 Upload Brainzy v2.0
    [Brainzy.sch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]
2018-09-30 Upload Brainzy v2.1
    [Brainzy.brd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]
2018-09-30 Upload Brainzy v3.0
    [Brainzy.brd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]
2018-09-30 Upload Brainzy v3.1
    [Brainzy.brd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]
2018-09-30 Upload Brainzy v3.2
    [Brainzy.brd, Brainzy.sch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]
2018-09-30 Upload Brainzy v3.2.1
    [Brainzy.brd, Brainzy.sch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]
2018-11-30 Add BOM file
    [BOM.xlsx]

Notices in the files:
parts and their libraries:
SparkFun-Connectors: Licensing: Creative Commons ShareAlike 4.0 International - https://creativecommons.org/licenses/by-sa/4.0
